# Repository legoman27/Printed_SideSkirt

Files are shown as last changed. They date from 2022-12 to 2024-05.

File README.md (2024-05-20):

# Printed_SideSkirt
A fully printed mod intended for a Voron Trident to relocate the electronics to the side of the printer with as little deviation from the standard BOM as possible.

Heavily inspired by by `kyledavis417#2007`'s [Trident sidepack mod](https://github.com/3DPrintingMods/VoronTrident-Sidepack).

Huge thanks to the Voron design team for everything!

#

Current design assumes a total thickness of side panel + foam tape = 3mm.

This mod could also be mounted on the rear of a trident, but this prevents access to the A/B belts at the rear of the gantry as well as moving the power inlet to the side of the machine, which may or may not be preferable.

Uses a completely stock Voron Spec Trident frame. Verticals are all the same length for 250 / 300 / 350, so the front and rear pieces will be the same for all sizes. 
LDO frames are taller, and will require modification --TODO!.

Total width of the side skirts is 90mm. 
the side skirts have provisions for an M3 heat set insert, and should be able to accept most side panel clips.
270 degree hinges mount to the side of the printer and are not compatible. any hinges that mount to the front should work just fine.

Total height of the lower skirts is 36mm.
The alternate lower skirts are optional, and were only created because I wanted to reduce the total z height of the printer slightly to fit in my workbench.
For smaller builds, it may be beneficial to use the standard full size Lower Skirts for more space for electronics, or if you want to retain the standard mini12864 screen. 
extended ribbon cables should be used in this case.

I originally created this for a trident with a 215mm^2 build area, so there is a narrower fan mount available if anyone else builds one for some reason.
All other sidepack pieces in this case are the same as a 250mm^2 build.

<p align="center">
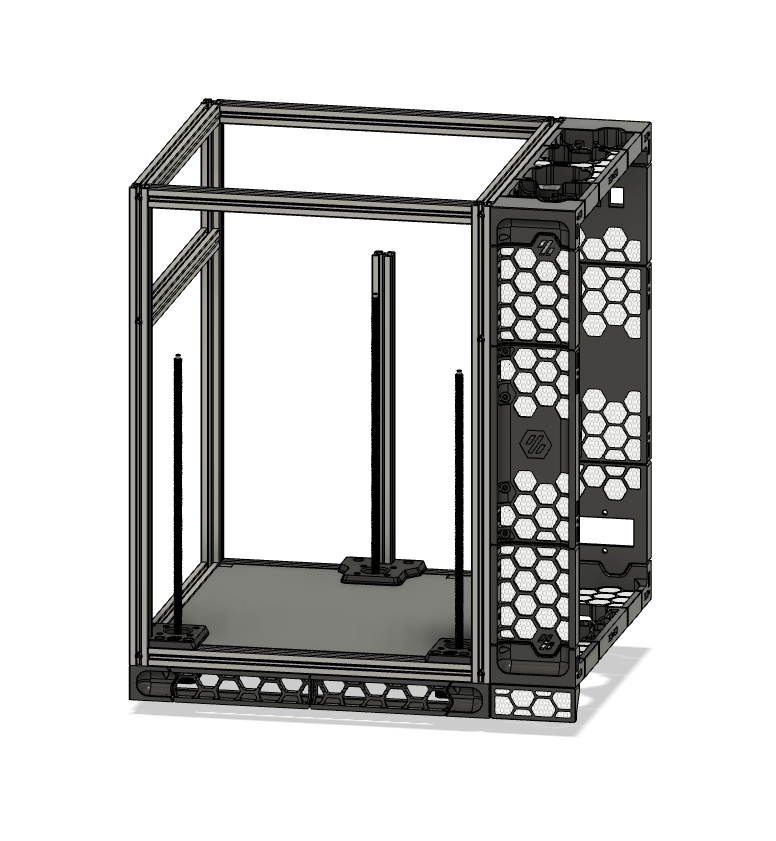
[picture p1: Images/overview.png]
  
</p>

# Future Plans
- [ ] finish lower skirts and update for standard frames
- [ ] add other power inlet types
- [x] ~~add support for 300 & 350 frames~~
- [ ] add support for LDO frames
- [ ] add some sort of display capability in the side skirt, mabye a btt TFT43 if it is at all possible to rotate the display by 90 degrees.



# EVERYTHNG BELOW THIS IS A WORK IN PROGRESS

# BOM Changes

+ 1x side panel of your size 250/300/350 - modified to allow for cable pass-through (OR PRINT the side panel)
+ 8x M5x10 BHCS
+ 8x M5 nut
+ 16x M3x8 SHCS
+ 12x M3x4x5 Heat set inserts

# Installation

FOAM TAPE IS REQUIRED BETWEEN THE SIDE PANEL AND THE FRAME. FRONT Z MOTOR WILL BIND ON THE PANEL WITHOUT CLEARANCE.

### SideSkirt mounted on the right side of the printer
- Z_rear parts & Cable chain mount are mirrored in X 
- Deck panel mounted upside down

### Lower Skirt corners
- For the front corners, install the captive M5 nut for the rubber feet before mounting to the frame. Inserting the nut after attaching to the frame is not possible due to clearance with the steppers.

### Corner Trim
- just stuck on with double sided tape

### DIN Rail mounts
- The din rails mount via M5x16 BHCS with captive nuts through the skirt

<p align="center">
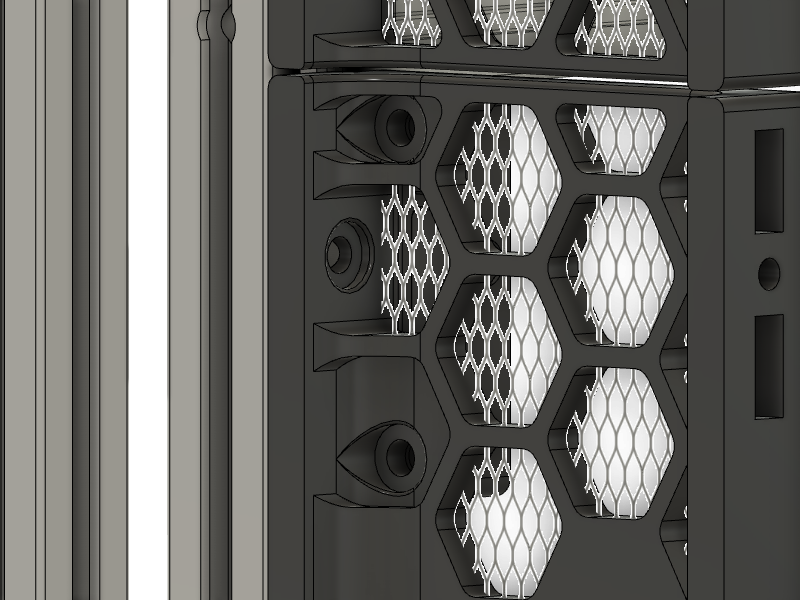
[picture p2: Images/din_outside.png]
  
</p>

<p align="center">
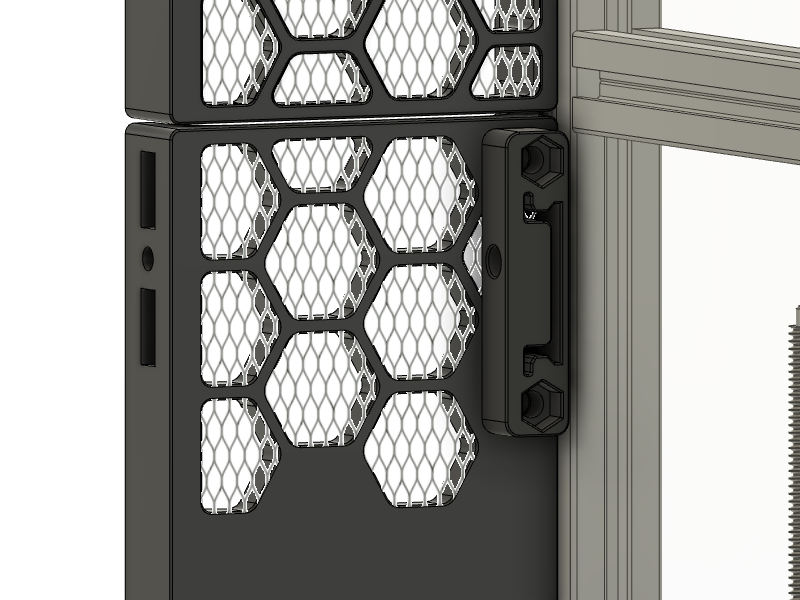
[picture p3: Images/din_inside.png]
  
</p>

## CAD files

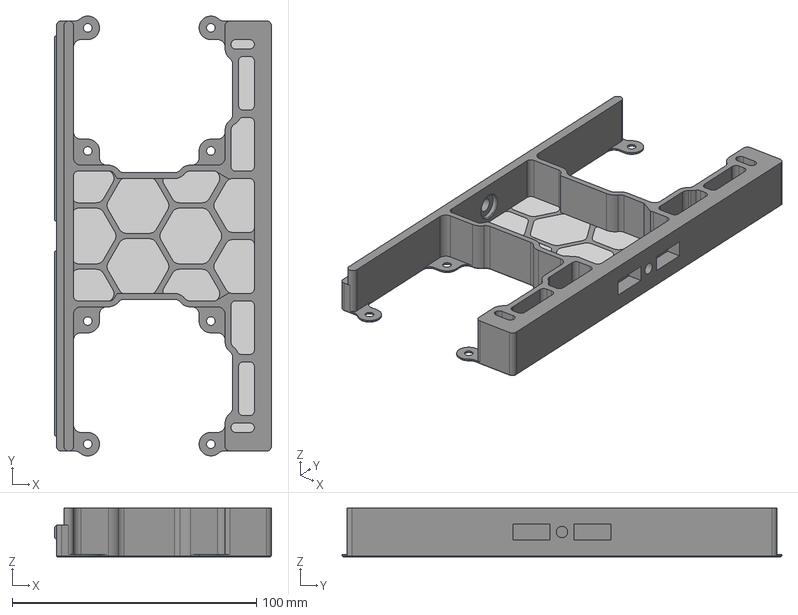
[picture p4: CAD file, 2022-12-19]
CAD/Printed SideSkirt Trident fan.step
88.8 x 180.0 x 20.0 mm

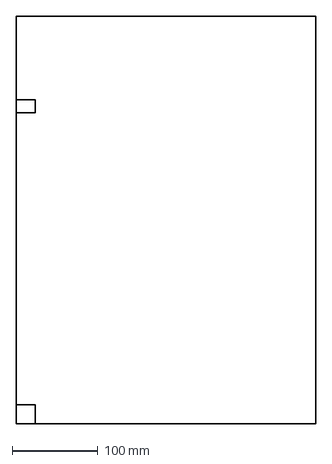
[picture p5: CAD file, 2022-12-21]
Panel DXFs/Modified Side panel 215.dxf
348.0 x 474.0 mm

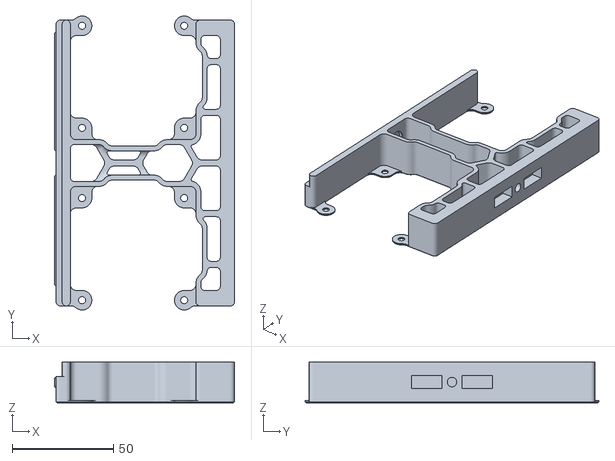
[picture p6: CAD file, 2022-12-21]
STLs/215mm specific/SideSkirt_Top_Bottom_Fan_215_x2.stl
88.8 x 145.0 x 20.0

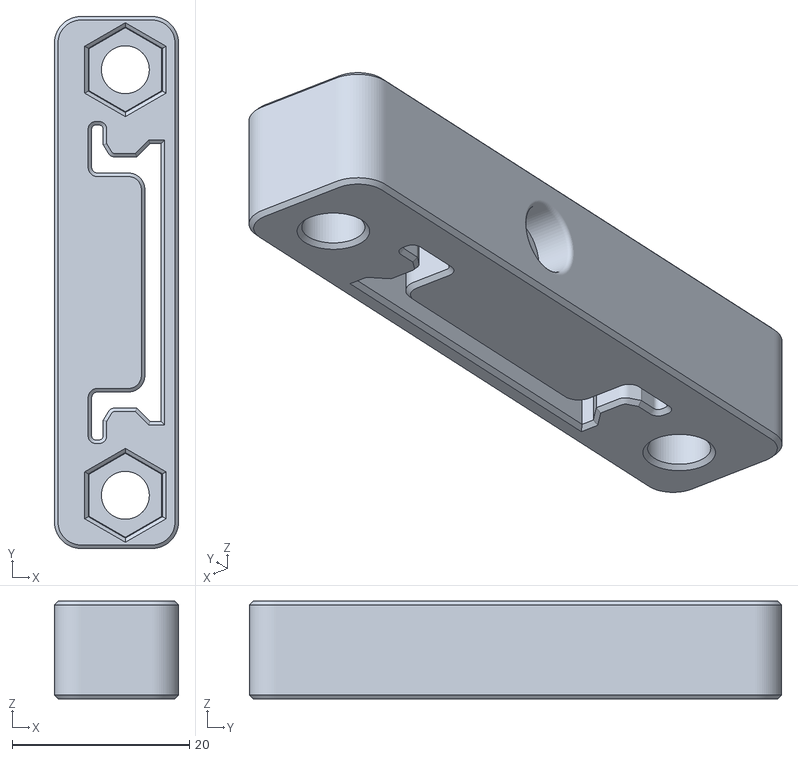
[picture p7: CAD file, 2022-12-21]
STLs/Electronics mounts/SideSkirt_DIN_mount_x4.stl
14.0 x 60.0 x 11.0

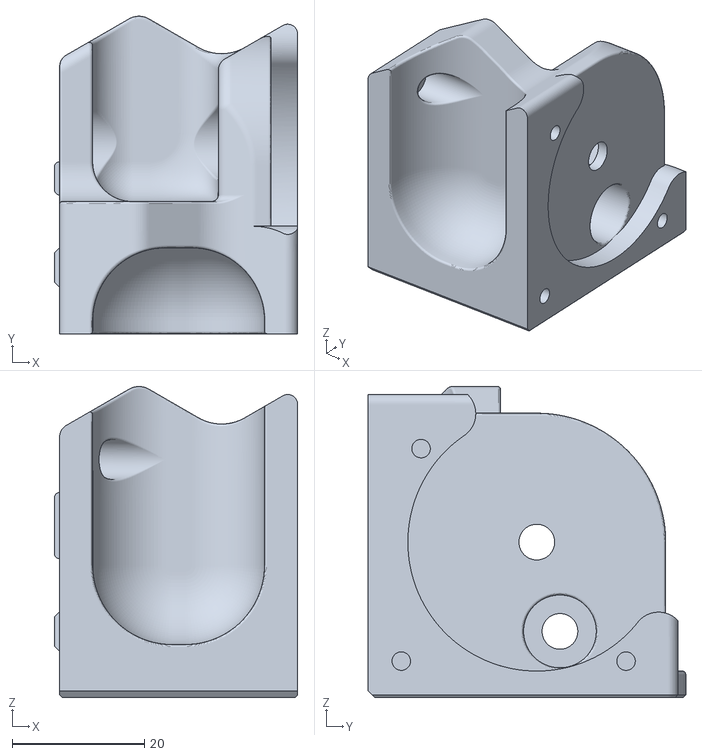
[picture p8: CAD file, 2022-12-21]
STLs/Lower skirts/SideSkirt_Lower_Corner_B_36mm.stl
36.8 x 48.0 x 47.0

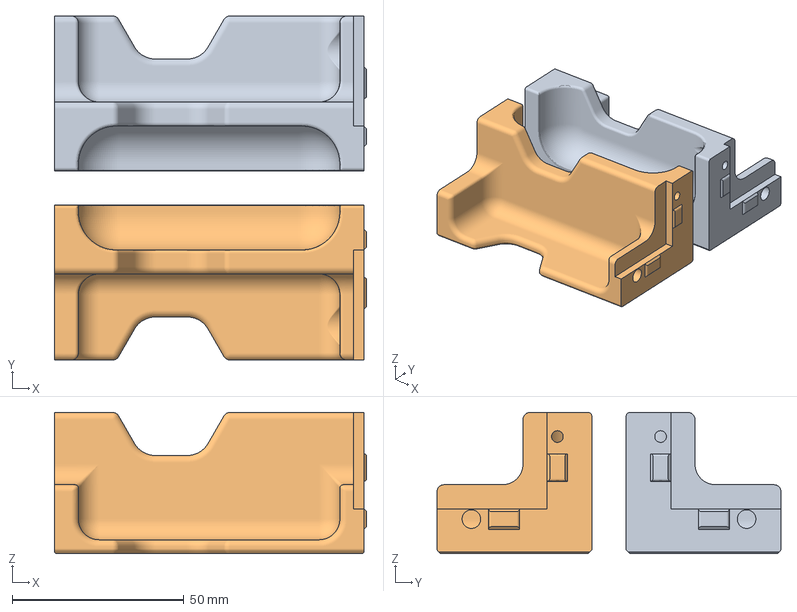
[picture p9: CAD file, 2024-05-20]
STLs/Side Skirts/Mesh skirts/SideSkirt_Corner_A&B_x2.3mf
90.8 x 100.0 x 41.0 mm

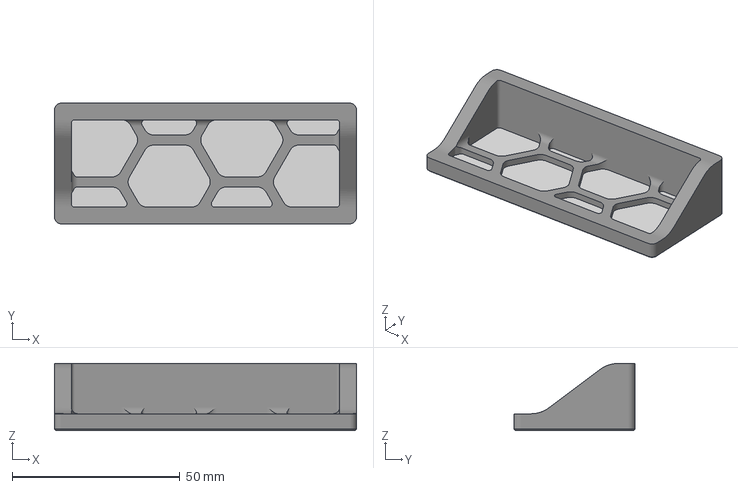
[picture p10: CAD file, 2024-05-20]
STLs/Trim/SideSkirt_Trim_36mmTo90mm_MESH.3mf
90.0 x 36.0 x 20.0 mm

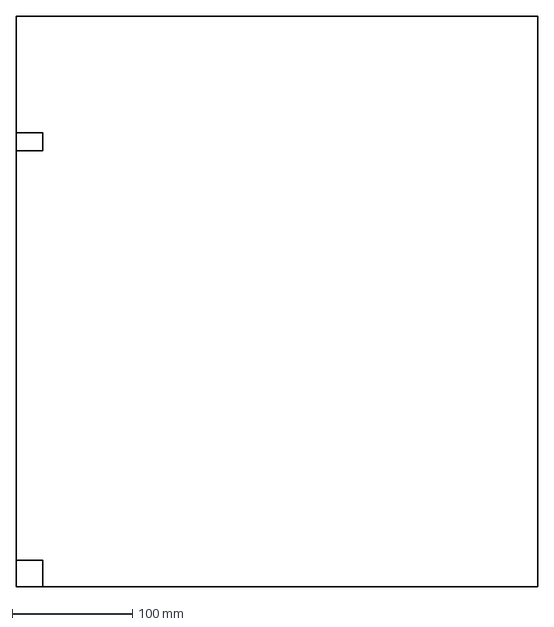
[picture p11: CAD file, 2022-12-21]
Panel DXFs/Modified Side panel 300.dxf
433.0 x 474.0 mm

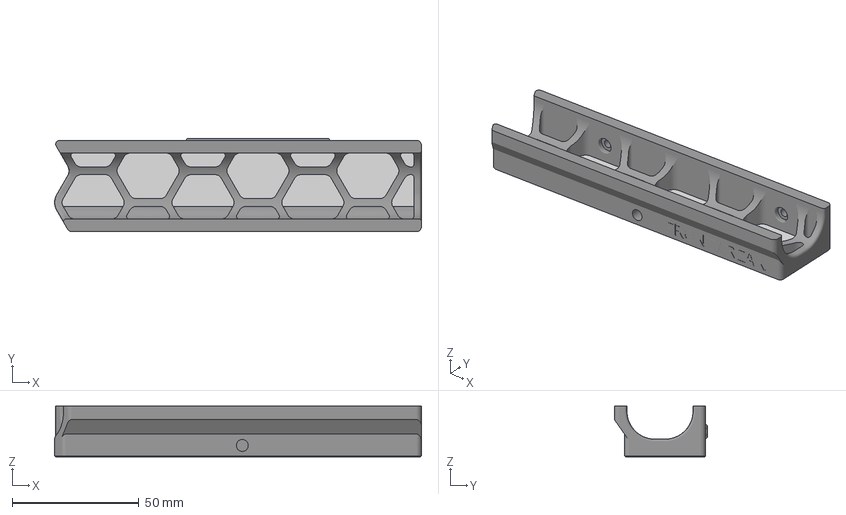
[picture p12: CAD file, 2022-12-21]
STLs/215mm specific/SideSkirt_Lower_Front_Rear_B_215_36mm_MESH_2x.3mf
144.6 x 36.8 x 20.0 mm

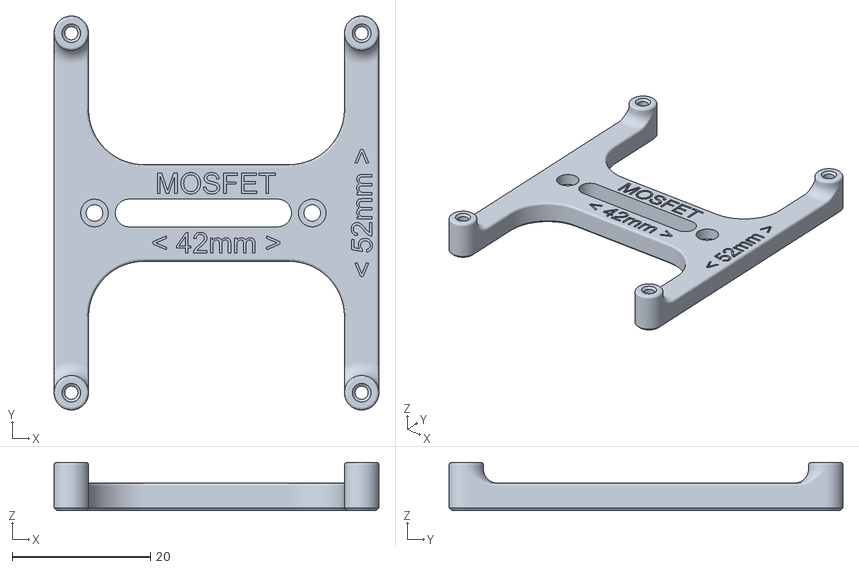
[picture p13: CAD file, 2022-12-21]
STLs/Electronics mounts/BTT_Mosfet_Mount.stl
47.0 x 57.0 x 7.00

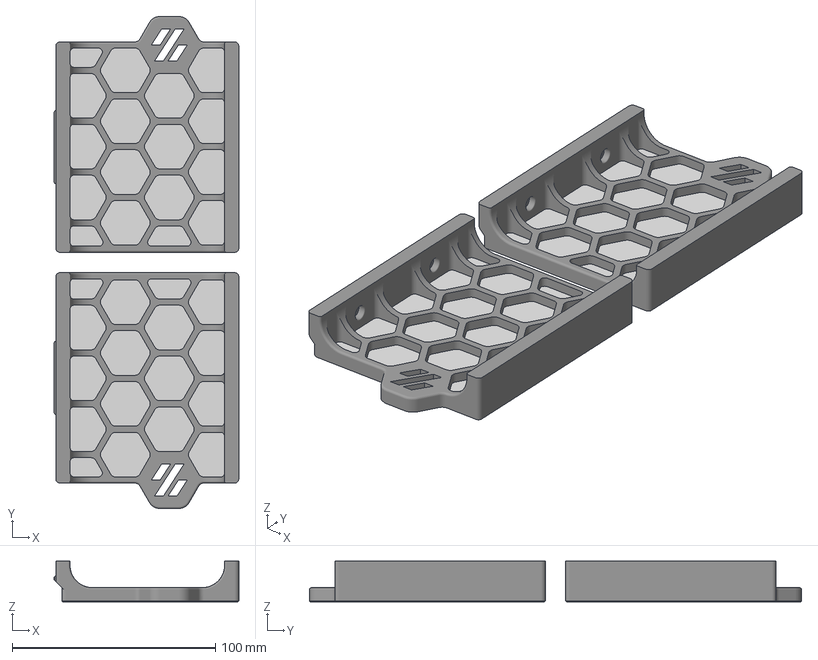
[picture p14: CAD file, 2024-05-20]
STLs/Side Skirts/Mesh skirts/SideSkirt_Front_A&B_x1.3mf
90.8 x 242.0 x 20.0 mm

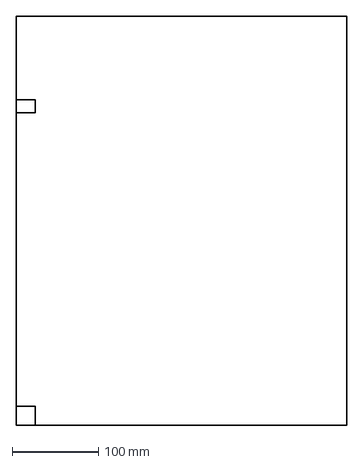
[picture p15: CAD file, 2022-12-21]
Panel DXFs/Modified Side panel 250.dxf
383.0 x 474.0 mm

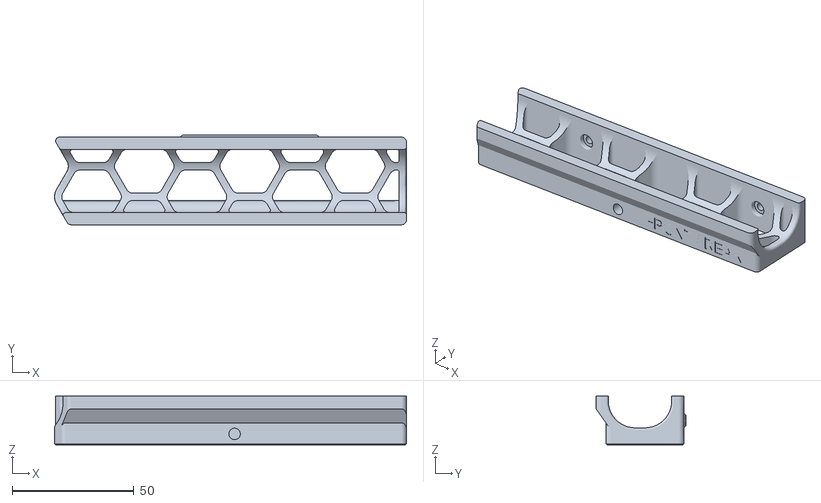
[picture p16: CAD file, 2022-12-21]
STLs/215mm specific/SideSkirt_Lower_Front_Rear_B_215_36mm_2x.stl
144.6 x 36.8 x 20.0

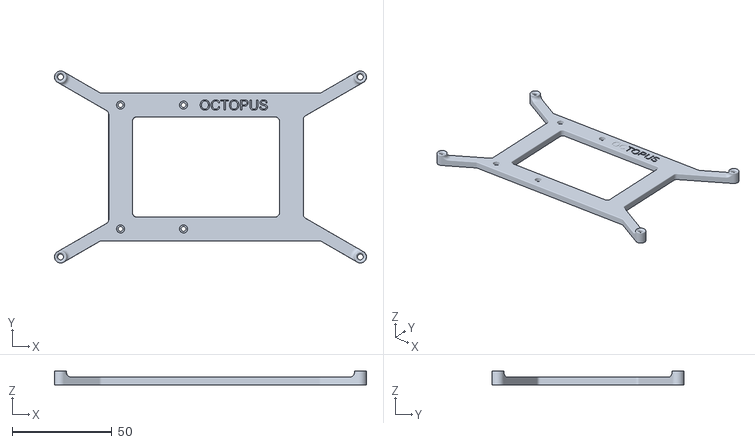
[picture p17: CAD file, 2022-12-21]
STLs/Electronics mounts/Octopus_Mount_Vertical_Offset.stl
156.1 x 96.1 x 7.00

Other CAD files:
STLs/Lower skirts/SideSkirt_Lower_Corner_A_36mm.stl
STLs/Side Skirts/Mesh skirts/SideSkirt_Front_Rear_Center_x2.3mf
Panel DXFs/Modified Side panel 350.dxf
STLs/215mm specific/SideSkirt_Lower_Side_B_215_36mm_MESH_2x.3mf
STLs/215mm specific/SideSkirt_Lower_Front_Rear_A_215_36mm_2x.stl
STLs/215mm specific/SideSkirt_Lower_Front_Rear_A_215_36mm_MESH_2x.3mf
STLs/215mm specific/SideSkirt_Lower_Side_A_215_36mm_2x.stl
STLs/215mm specific/SideSkirt_Lower_Side_A_215_36mm_MESH_2x.3mf
STLs/215mm specific/SideSkirt_Lower_Side_B_215_36mm_2x.stl
STLs/215mm specific/SideSkirt_Top_Bottom_Fan_215_MESH_x2.3mf
STLs/Side Skirts/Mesh skirts/SideSkirt_Rear_Keystone_MESHx1.3mf
STLs/Side Skirts/Mesh skirts/SideSkirt_Rear_inlet_IEC320_MESHx1.3mf
STLs/Side Skirts/Mesh skirts/SideSkirt_Top_Bottom_A_250_MESH_x2.3mf
STLs/Side Skirts/Mesh skirts/SideSkirt_Top_Bottom_A_300_MESH_x2.3mf
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

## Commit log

2022-12-19 215MM trident SideSkirt
    lower skirt includes front center skirts
    lower side skirts have not been created
2022-12-19 (untested) Add fan skirt for 250MM Builds
    My designs were initially based on a 215x215x250 sized frame, this adds a fan skirt compatible with 250mm frames
    [SideSkirt_Trident_Fan_Skirt_Infill_250.step]
2022-12-21 deleted to rename file
    [SideSkirt_Trident_Fan_Skirt_Infill_250.step]
2022-12-21 File renamed
    [Printed SideSkirt Trident fan.step]
2022-12-21 Initial commit
    side skirt files for 215 & 250 mm builds
    lower skirt files for 215 builds
    [BTT_Mosfet_Mount.stl, Octopus_Mount_Vertical_Offset.stl, SideSkirt_Corner_A_2x.stl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]
2024-05-20 300 & 350 sideskirts completed
    finished sideskirts for 300 & 350 frames
    mounting point for 250mm top_bottom A/B moved to be closer to center of part
    [SideSkirt_Top_Bottom_A_250_MESH_x2.3mf, SideSkirt_Top_Bottom_A_300_MESH_x2.3mf, SideSkirt_Top_Bottom_A_350_MESH_x2.3mf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]
